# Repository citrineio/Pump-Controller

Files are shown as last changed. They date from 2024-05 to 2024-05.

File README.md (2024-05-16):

# Pump-Controller
This is the next version of the previously featured AC Switch. This is an IOT device that can turn normal water pumps smart. This device is meant to detect plumbing issues and automatically or allow the user to act. 
pump controller 2

## Features

 1. A wireless microcontroller (ESP32-C3-WROOM-02-N4) for remote monitoring and control of the pump.
 2.  40A SPDT relay with Quick Connect contacts (AZ2100-1CE-5DEF).
 3. 20A current transformer (ZMCT102) to detect when the pump is on by measuring motor current.
 4. A JST connector (B4B-PH-K) for a [pressure sensor](https://www.digikey.com/en/products/detail/seeed-technology-co-ltd/114991178/7387419)  to identify if the pump is pumping air.
 5. An AC/DC converter (PBO-5C-5 or equivalent) to supply power from an outlet.

## Block Diagram



## Future improvements

 1. Replace spring clamp terminal blocks with pluggable or screw terminals.
 2. Replace the JST connector with a pluggable terminal block.
 3. Replace TC2050 footprint and UART JST connector with 2.54mm footprints for use with a pogo pin probe clip (e.g. [This](https://www.adafruit.com/product/5434)).
 4. The board was designed with a specific enclosure in mind. Future revisions will have their own custom designed enclosure.
 5. Tagconnect cables without clamps are very inconvenient. 

Please let me know if you have any suggestions or improvements

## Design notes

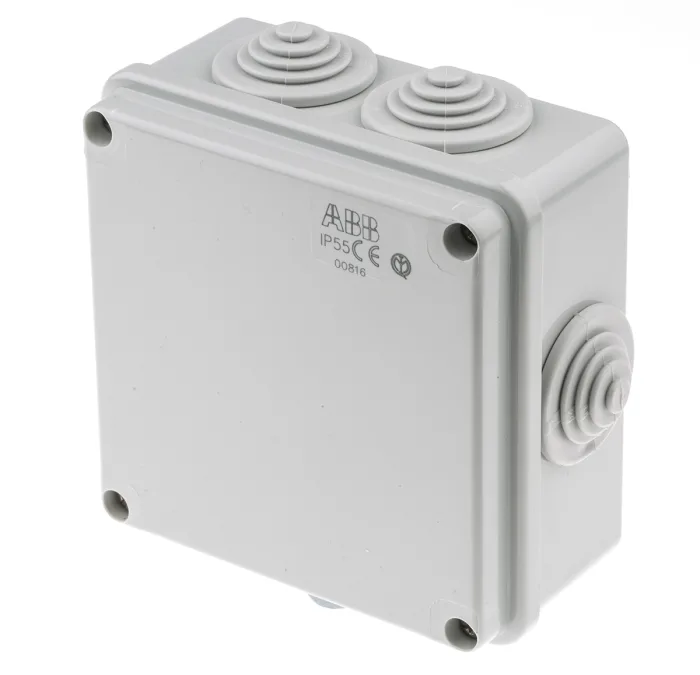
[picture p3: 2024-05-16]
V3.0/Mechanicals/Enclosure/F0454993-01.webp

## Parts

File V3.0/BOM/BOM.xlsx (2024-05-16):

# | Reference | Qty | Value | Footprint | DNP | Manufacturer | PN
1 | C3, C4, C5, C6 | 4 | 1u | parts:CAPC1608X90N_SAMSUNG |  | Samsung Electro-Mechanics | CL10B105KO8NNNC
2 | C7, C8 | 2 | 6P | parts:CAPC1608X90N_SAMSUNG |  | Samsung Electro-Mechanics | CL10C060DB8NNNC
3 | D1 | 1 | 1N4007FL | parts:CR_SOD-123FL_SME |  | SMC Diode Solutions | 1N4007FL
4 | H1, H2 | 2 | MountingHole | MountingHole:MountingHole_2.7mm_M2.5
5 | J1 | 1 | TB002-500-03BE | CUI_TB002-500-03BE |  | CUI Devices | TB002-500-03BE
6 | J2 | 1 | Conn_01x14 | Connector_PinHeader_2.54mm:PinHeader_1x08_P2.54mm_Vertical |  | Sullins Connector Solutions | PPTC141LFBN-RC
7 | K1 | 1 | G5LE-14 DC5 | Relay_THT:Relay_SPDT_Omron-G5LE-1 |  | OMRON | G5LE-14 DC5
8 | PS101 | 1 | HLK-PM01 | Converter_ACDC:Converter_ACDC_HiLink_HLK-PMxx |  | HI-LINK | HLK-PM01
9 | Q1 | 1 | Q_NMOS_GSD | parts:DMN65D8L-7_MOSFET |  | Diodes Incorporated | DMN65D8L-7
10 | R2, R3, R4 | 3 | 10K | parts:RESC1607X60N |  | YAGEO | RC0603JR-0710KL
11 | R5 | 1 | 10K | parts:RESC1607X60N | DNP | YAGEO | RC0603JR-0710KL
12 | RV1 | 1 | S14K350 | parts:VARS_B72214S_15P5X5P6-7P5-2P2_TDK |  | TDK | B72214S0351K101
13 | SW1 | 1 | TS-1187A-B-A-B | SW_TS-1187A-B-A-B |  | XKB Industrial Precision | TS-1187A-B-A-B
14 | SW2 | 1 | SW_SPDT | parts:SW_JS102011SAQN |  | C&K | JS102011SAQN
15 | U2 | 1 | AP2112K-3.3TRG1 | Package_TO_SOT_SMD:SOT-23-5 |  | Diodes Incorporated | AP2112K-3.3TRG1
16 | U3 | 1 | ESP32-C3-MINI-1U-H4 | parts:XCVR_ESP32-C3-MINI-1U-N4 |  | Espressif Systems | ESP32-C3-MINI-1U-H4
17 | Y1 | 1 | 32K768 | parts:XTAL_FC-135R_32.7680KA-AG0 |  | EPSON | FC-135R 32.7680KA-AG0

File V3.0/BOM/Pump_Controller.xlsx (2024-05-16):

Reference | Value | Qty | DNP | Manufacturer | Part Number
C101,C102,C103,C104,C105,C106,C108,C109,C115 | 1u | 9 |  | Samsung Electro-Mechanics | C15849
C110 | 10u | 1 |  | Samsung Electro-Mechanics | C96446
C111 | 22u | 1 |  | EPCOS - TDK Electronics | C160173
C112 | 470u | 1 |  | Kemet | C2887210
C113 | 100u | 1 |  | KEMET | C109392
C114 | 1n | 1 |  | Samsung | C651029
CR101 | SMBJ7.0CA-13-F | 1 |  | Diodes Incorporated | C7420377
D101 | 1N4007FL | 1 |  | SMC Diode Solutions | C64898
F101 | 56000001019 | 1 |  | Littelfuse Inc. | C206886
J101 | Screw_Terminal_01x02 | 1
J102,J105 | B4B-PH-K | 2 |  | JST | C131334
K101 | AZ2100-1CE-5DEF | 1 |  | American Zettler | C187900
L101 | 4m7 | 1 |  | Bourns | C6341414
L102 | 4u7 | 1 |  | Taiyo Yuden | C32684
PS101 | PBO-5C-5 | 1 |  | CUI Inc. | C784062
Q101,Q102,Q103,Q104 | C20917 | 4 |  | Alpha & Omega Semicon | C20917
R101,R103,R104,R109 | 10K | 4 |  | UNI-ROYAL(Uniroyal Elec) | C25804
R102 | 0R | 1 | DNP | UNI-ROYAL(Uniroyal Elec) | C21189
R106,R107,R108,R114,R115,R116 | 2k2 | 6 |  | UNI-ROYAL(Uniroyal Elec) | C4190
R113 | 12R | 1 |  | Yageo | C3013863
R118 | 68R | 1 |  | UNI-ROYAL(Uniroyal Elec) | C27592
R119 | 0R | 1 |  | UNI-ROYAL(Uniroyal Elec) | C21189
RV101 | B72214S0351K101 | 1 |  | B72214S0351K101 | B72214S0351K101
SW101 | SW_SPDT | 1 |  | XKB Connectivity | SS-12D10L3
SW102 | TS-1187A-B-A-B | 1 |  | XKB Industrial Precision | TS-1187A-B-A-B
TR102 | ZMCT102 | 1 |  | Qingxian Zeming Langxi Electronic | ZMCT102
U101 | ESP32-C3-WROOM | 1 |  | Espressif Systems | ESP32-C3-WROOM-02-N4
U102 | AP2112K-3.3 | 1 |  | Diodes Incorporated | AP2112K-3.3
U103 | ADS1115IDGSR | 1 |  | Texas Instruments | ADS1115IDGSR

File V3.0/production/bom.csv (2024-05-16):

Designator | Footprint | Quantity | Value | LCSC Part #
C101, C102, C103, C104, C105, C106, C108, C109, C115 | CL10A | 9 | 1u
C110 | CL10A | 1 | 10u
C111 | CP_Radial_D12.5mm_P5.00mm | 1 | 22u
C112 | CP_Radial_D6.3mm_P2.50mm | 1 | 470u
C113 | CP_Radial_D6.3mm_P2.50mm | 1 | 100u
C114 | CAP_CL31_SAM | 1 | 1n
CR101 | SMB_DIO | 1 | SMBJ7.0CA-13-F
D101 | SODFL3618X110N | 1 | 1N4007FL
F101 | FUSE_560_1019_LTF | 1 | 56000001019
H102, H103, H104 | MountingHole_3.2mm_M3 | 3 | MountingHole
J101 | CONN-TH_2P-P5.08_WJ142V-5.08-2P | 1 | Screw_Terminal_01x02
J102, J105 | JST_B4B-PH-K | 2 | B4B-PH-K
J103 | TAG-CONNECT_TC2050-IDC-NL | 1 | TC2050-IDC-NL
K101 | AZ2100-1CE-5DEF | 1 | AZ2100-1CE-5DEF
L101 | IND_RLB9012-472KL | 1 | 4m7
L102 | IND_HL4R7M_TAY | 1 | 4u7
PS101 | CONV_PBO-5C-5 | 1 | PBO-5C-5
Q101, Q102, Q103, Q104 | SOT-23 | 4 | DMG2302UK
R101, R103, R104, R109 | RESC1607X60N | 4 | 10K
R102, R119 | RESC1607X60N | 2 | 0R
R106, R107, R108, R114, R115, R116 | RESC1607X60N | 6 | 2k2
R113 | YAG_FMP200_YAG | 1 | 12R
R118 | RESC1607X60N | 1 | 68R
RV101 | VAR_B72214S0351K101 | 1 | B72214S0351K101
SW101 | SS12D10L3 | 1 | SW_SPDT
SW102 | SW_TS-1187A-B-A-B | 1 | TS-1187A-B-A-B
TR102 | zmct102 | 1 | ZMCT102
U101 | XCVR_ESP32-C3-WROOM-02U-N4 | 1 | ESP32-C3-WROOM
U102 | SOT95P285X140-5N | 1 | AP2112K-3.3
U103 | ADS1115_SOP50P490X110-10N | 1 | ADS1115IDGSR

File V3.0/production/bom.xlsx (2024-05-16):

Designator | Footprint | Quantity | Value | LCSC Part #
C101, C102, C103, C104, C105, C106, C108, C109, C115 | CL10A | 9 | 1u | C59782
C110 | CL10A | 1 | 10u | C96446
C111 | CP_Radial_D12.5mm_P5.00mm | 1 | 22u | C473184
C112 | CP_Radial_D6.3mm_P2.50mm | 1 | 470u | C2898811
C113 | CP_Radial_D6.3mm_P2.50mm | 1 | 100u | C495099
C114 | CAP_CL31_SAM | 1 | 1n | C3841467
CR101 | SMB_DIO | 1 | SMBJ7.0CA-13-F | C135095
D101 | SODFL3618X110N | 1 | 1N4007FL | C250817
F101 | FUSE_560_1019_LTF | 1 | 56000001019 | C142909
H102, H103, H104 | MountingHole_3.2mm_M3 | 3 | MountingHole
J101 | CONN-TH_2P-P5.08_WJ142V-5.08-2P | 1 |  | WJ142V-5.08-2P
J102, J105 | JST_B4B-PH-K | 2 | B4B-PH-K | C265289
J103 | TAG-CONNECT_TC2050-IDC-NL | 1 | TC2050-IDC-NL
K101 | AZ2100-1CE-5DEF | 1 | AZ2100-1CE-5DEF | AZ2100-1CE-5DEF
L101 | IND_RLB9012-472KL | 1 | 4m7 | RLB9012-472KL
L102 | IND_HL4R7M_TAY | 1 | 4u7 | LSXBD6060WHL4R7M
PS101 | CONV_PBO-5C-5 | 1 | PBO-5C-5 | C784062
Q101, Q102, Q103, Q104 | SOT-23 | 4 | DMG2302UK | C20917
R101, R103, R104, R109 | RESC1607X60N | 4 | 10K | C25804
R106, R107, R108, R114, R115, R116 | RESC1607X60N | 6 | 2k2 | C4190
R113 | YAG_FMP200_YAG | 1 | 12R | FMP200JR-52-12R
R118 | RESC1607X60N | 1 | 68R | C27592
R119 | RESC1607X60N | 1 | 0R | C21189
RV101 | VAR_B72214S0351K101 | 1 | B72214S0351K101 | B72214S0351K101
SW101 | SS12D10L3 | 1 | SW_SPDT | C319013
SW102 | SW_TS-1187A-B-A-B | 1 | TS-1187A-B-A-B | C318884
TR102 | zmct102 | 1 | ZMCT102 | C84213
U101 | XCVR_ESP32-C3-WROOM-02U-N4 | 1 | ESP32-C3-WROOM | C2934560
U102 | SOT95P285X140-5N | 1 | AP2112K-3.3 | C51118
U103 | ADS1115_SOP50P490X110-10N | 1 | ADS1115IDGSR | C37593

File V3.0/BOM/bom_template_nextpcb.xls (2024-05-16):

Manufacturer Part Number* | Qty* | Designator* | Customer Supply | Customer Remark
CL10B105KO8NNNC | 9 | C101,C102,C103,C104,C105,C106,C108,C109,C115
CL10A106MA8NRNC | 1 | C110
B43821F5226M000 | 1 | C111
SPZ1CM471E11O00RAXXX | 1 | C112
ESL107M035AE3AA | 1 | C113
CL31B102KHFNFNE | 1 | C114
SMBJ7.0CA-13-F | 1 | CR101
1N4007FL | 1 | D101
56000001019 | 1 | F101
WJ142V-5.08-2P | 1 | J101
B4B-PH-K | 2 | J102,J105
AZ2100-1CE-5DEF | 1 | K101
RLB9012-472KL | 1 | L101
LSXBD6060WHL4R7M | 1 | L102
LS05-13B05R3 | 1 | PS101
AO3400A | 4 | Q101,Q102,Q103,Q104
0603WAF1002T5E | 4 | R101,R103,R104,R109
0603WAF0000T5E | 1 | R102 | DNP
0603WAF2201T5E | 6 | R106,R107,R108,R114,R115,R116
FMP200JR-52-12R | 1 | R113
0603WAF680JT5E | 1 | R118
0603WAF0000T5E | 1 | R119
B72214S0351K101 | 1 | RV101
SS-12D10L3 | 1 | SW101
TS-1187A-B-A-B | 1 | SW102
ZMCT102 | 1 | TR102
ESP32-C3-WROOM-02-N4 | 1 | U101
AP2112K-3.3TRG1 | 1 | U102
ADS1115IDGSR | 1 | U103

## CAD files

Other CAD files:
V3.0/Mechanicals/Enclosure/LK-DR56.dwg
V3.0/Mechanicals/Enclosure/LK-PLC24 25B.dwg

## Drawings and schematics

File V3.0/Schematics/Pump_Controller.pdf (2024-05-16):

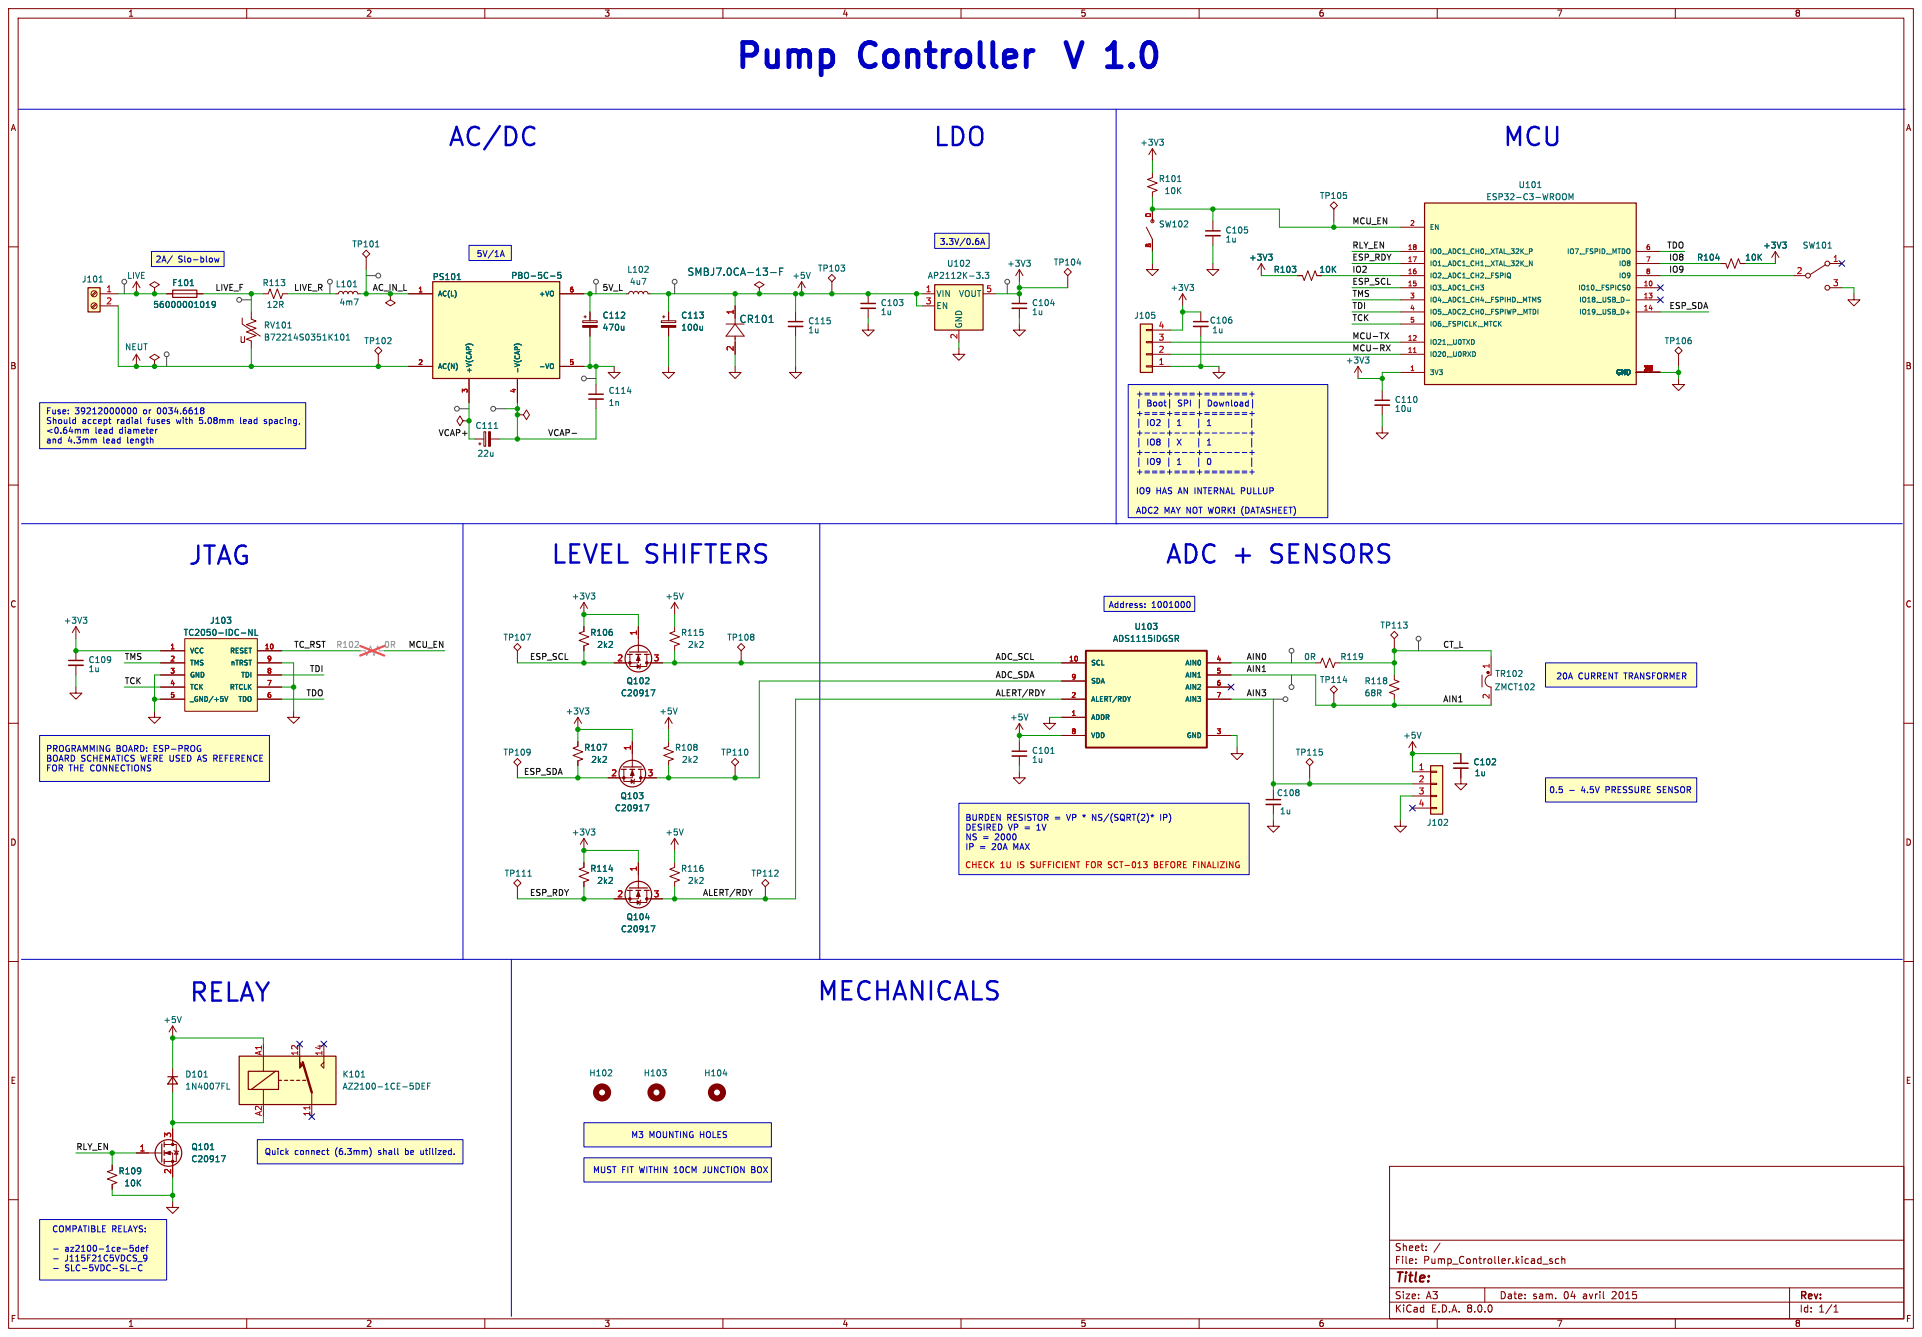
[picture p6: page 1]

IP = 20A MAX Pump Controller

IO9 HAS AN INTERNAL PULLUP
ADC + SENSORS

ADC2 MAY NOT WORK! (DATASHEET) M3 MOUNTING HOLES

PROGRAMMING BOARD: ESP-PROG
BOARD SCHEMATICS WERE USED AS REFERENCE

MUST FIT WITHIN 10CM JUNCTION BOX

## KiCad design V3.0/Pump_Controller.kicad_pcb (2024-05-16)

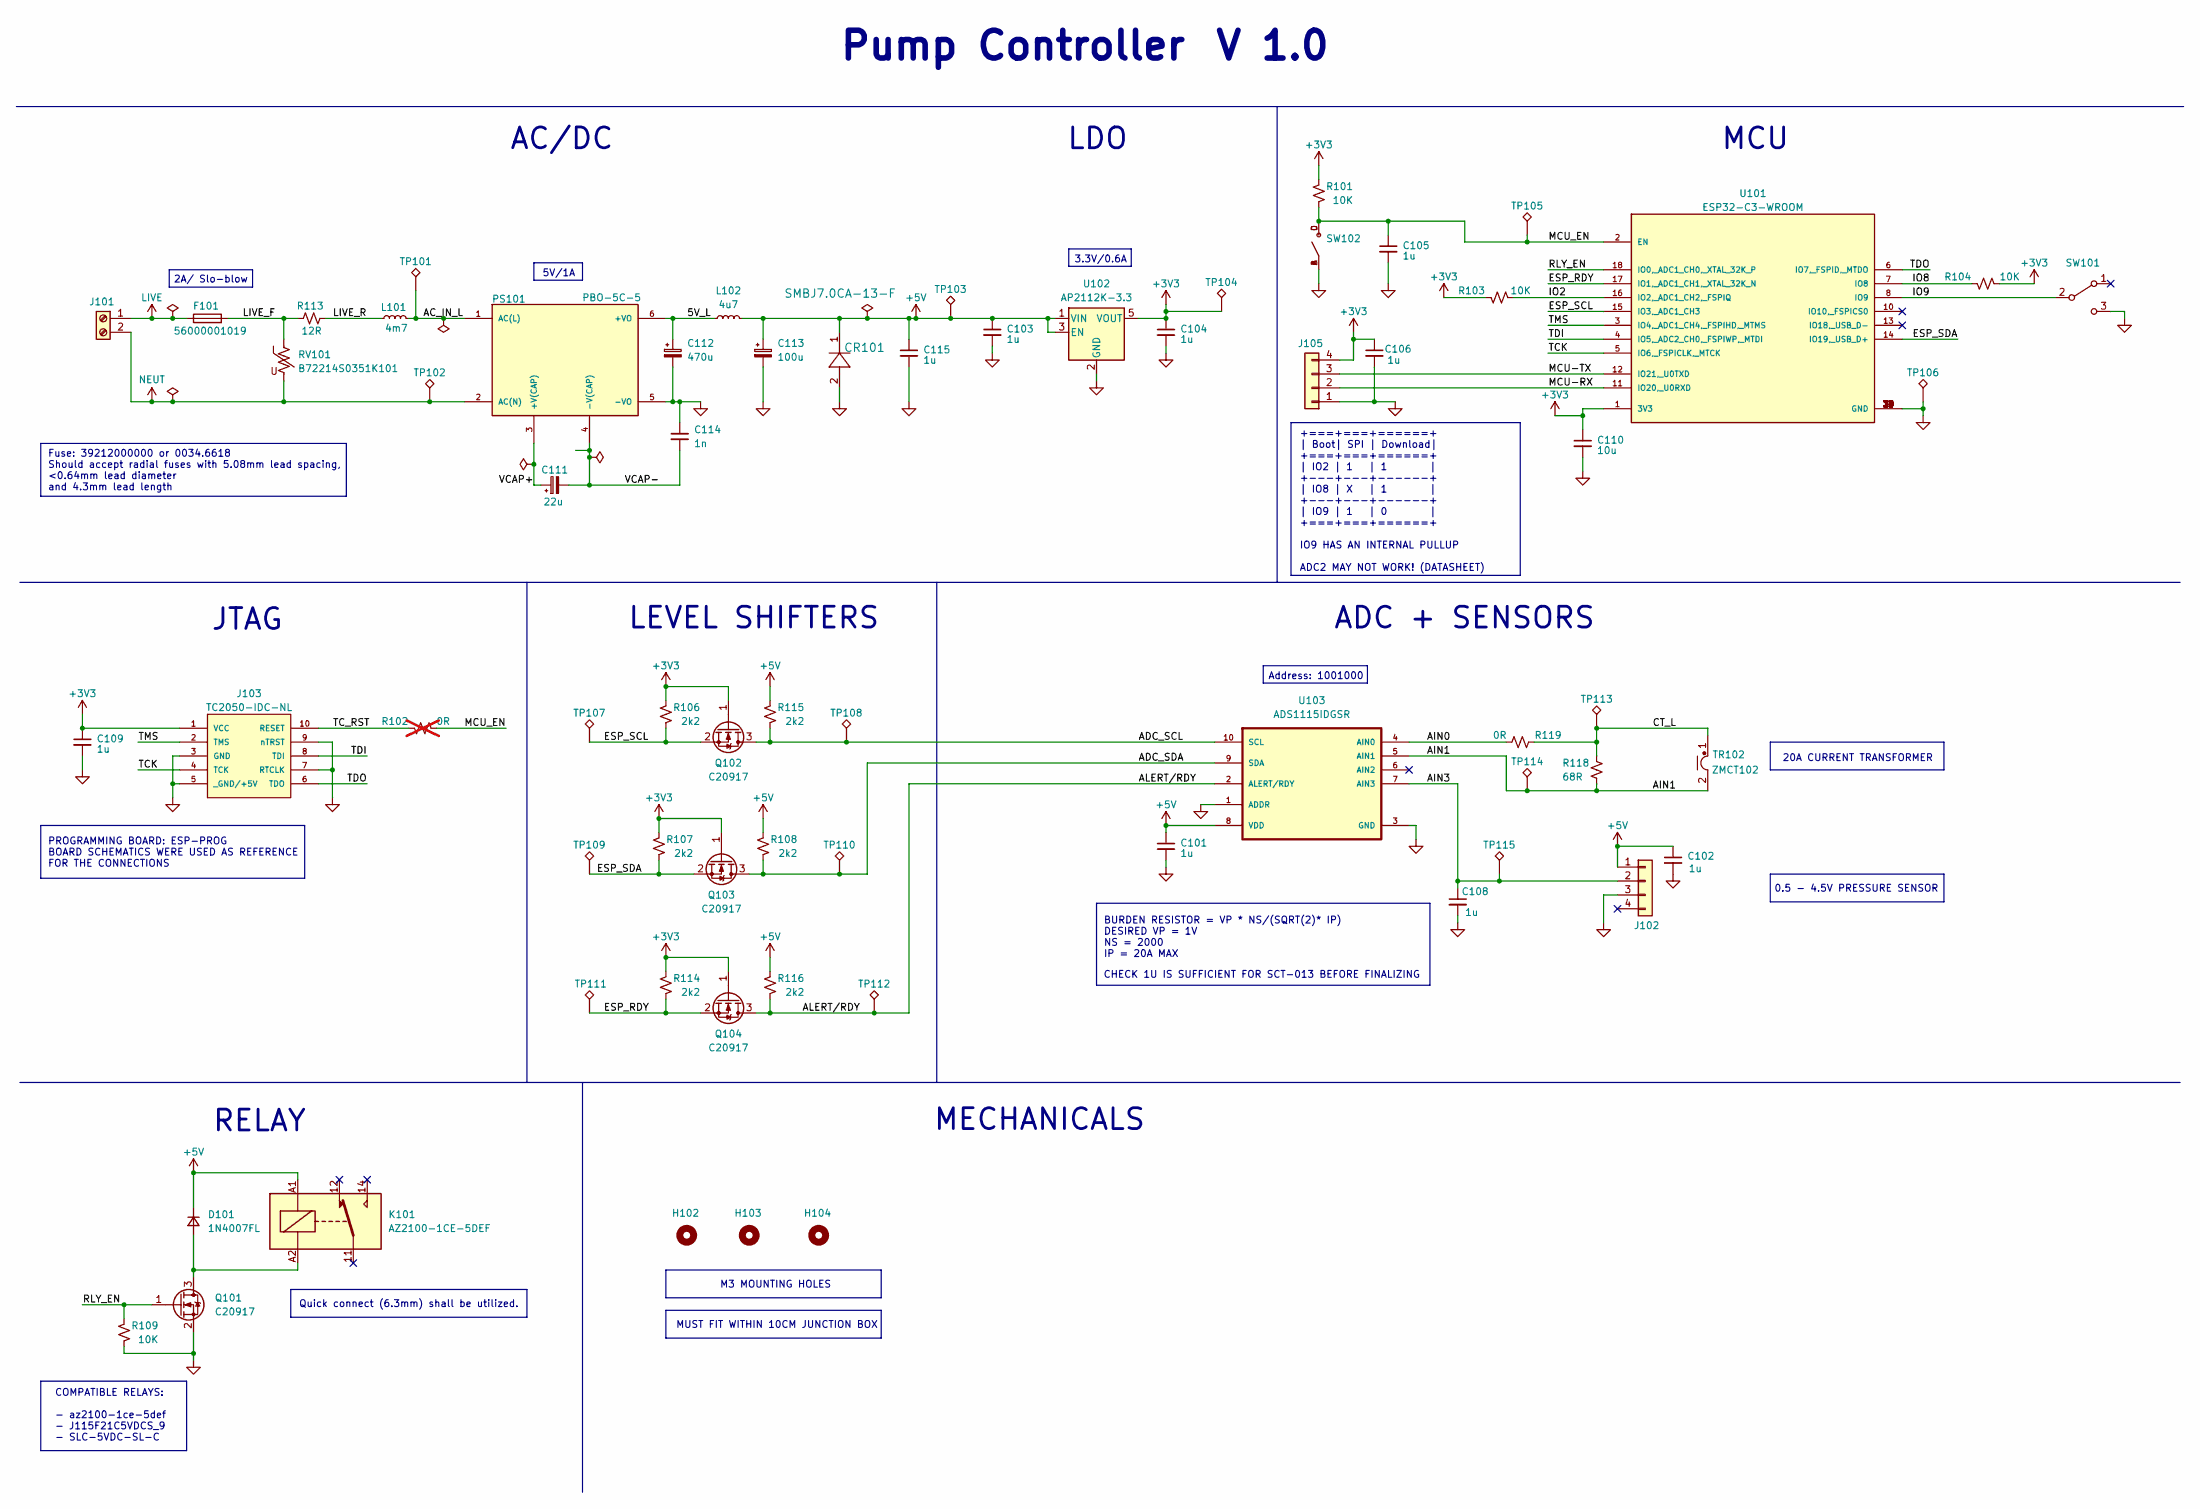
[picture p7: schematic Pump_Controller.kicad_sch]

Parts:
C101, C102, C103, C104, C105, C106, C108, C109, C115: 1u; CL10A; Part Number CL10B105KO8NNNC - C59782
C110: 10u; CL10A; Part Number CL10A106MA8NRNC - C96446
C111: 22u; CP_Radial_D12.5mm_P5.00mm; Part Number B43821F5226M000
C112: 470u; CP_Radial_D6.3mm_P2.50mm; Part Number A750EQ477M1CAAE015
C113: 100u; CP_Radial_D6.3mm_P2.50mm; Part Number ESL107M035AE3AA
C114: 1n; CAP_CL31_SAM; Part Number CL31B102KHFNFNE
CR101: SMBJ7.0CA-13-F; SMB_DIO; Part Number SMBJ7.0CA-13-F
D101: 1N4007FL; SODFL3618X110N; Part Number 1N4007FL
F101: 56000001019; FUSE_560_1019_LTF; Part Number 56000001019
H102, H103, H104: MountingHole; MountingHole_3.2mm_M3
J101: Screw_Terminal_01x02; CONN-TH_2P-P5.08_WJ142V-5.08-2P
J102, J105: B4B-PH-K; JST_B4B-PH-K; Part Number B4B-PH-K
J103: TC2050-IDC-NL; TAG-CONNECT_TC2050-IDC-NL
K101: AZ2100-1CE-5DEF; Part Number AZ2100-1CE-5DEF
L101: 4m7; IND_RLB9012-472KL; Part Number RLB9012-472KL
L102: 4u7; IND_HL4R7M_TAY; Part Number LSXBD6060WHL4R7M
PS101: PBO-5C-5; CONV_PBO-5C-5; Part Number PBO-5C-5
Q101, Q102, Q103, Q104: C20917; SOT-23; Part Number AO3400A
R101, R103, R104, R109: 10K; RESC1607X60N; Part Number 0603WAF1002T5E - C25804
R102: 0R; RESC1607X60N; Part Number 0603WAF0000T5E - C21189; not fitted
R106, R107, R108, R114, R115, R116: 2k2; RESC1607X60N; Part Number 0603WAF2201T5E- C4190
R113: 12R; YAG_FMP200_YAG; Part Number FMP200JR-52-12R
R118: 68R; RESC1607X60N; Part Number 0603WAF680JT5E- C27592
R119: 0R; RESC1607X60N; Part Number 0603WAF0000T5E - C21189
RV101: B72214S0351K101; VAR_B72214S0351K101; Part Number B72214S0351K101
SW101: SW_SPDT; SS12D10L3; Part Number SS-12D10L3
SW102: TS-1187A-B-A-B; SW_TS-1187A-B-A-B; Part Number TS-1187A-B-A-B
TP101, TP102: TestPoint_Alt; TestPoint_Loop_D2.50mm_Drill1.0mm
TP103, TP104, TP105, TP106, TP107, TP108, TP109, TP110, TP111, TP112, TP113, TP114, TP115: TestPoint_Alt; TestPoint_Pad_1.5x1.5mm
TR102: ZMCT102; zmct102; Part Number ZMCT102
U101: ESP32-C3-WROOM; XCVR_ESP32-C3-WROOM-02U-N4; Part Number ESP32-C3-WROOM-02-N4
U102: AP2112K-3.3; SOT95P285X140-5N; Part Number AP2112K-3.3
U103: ADS1115IDGSR; ADS1115_SOP50P490X110-10N; Part Number ADS1115IDGSR

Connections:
+3V3: C104.1, C106.1, C109.1, C110.1, J103.1 (VCC), J105.4, Q102.1 (G), Q103.1 (G), Q104.1 (G), R101.1, R103.1, R104.2, R106.1, R107.1, R114.1, TP104.1, U101.1 (3V3), U102.5 (VOUT)
+5V: C101.1, C102.1, C103.1, C113.1, C115.1, CR101.1, D101.1 (K), J102.1, K101.A1, L102.2, R108.1, R115.1, R116.1, TP103.1, U102.1 (VIN), U102.3 (EN), U103.8 (VDD)
/5V_L: C112.1, L102.1, PS101.6 (+VO)
/AC_IN_L: L101.2, PS101.1 (AC(L)), TP101.1
/ADC_SCL: Q102.3 (D), R115.2, TP108.1, U103.10 (SCL)
/ADC_SDA: Q103.3 (D), R108.2, TP110.1, U103.9 (SDA)
/AIN0: R119.2, U103.4 (AIN0)
/AIN1: R118.2, TP114.1, TR102.2, U103.5 (AIN1)
/AIN3: C108.1, J102.2, TP115.1, U103.7 (AIN3)
/ALERT/RDY: Q104.3 (D), R116.2, TP112.1, U103.2 (ALERT/RDY)
/CT_L: R118.1, R119.1, TP113.1, TR102.1
/ESP_RDY: Q104.2 (S), R114.2, TP111.1, U101.17 (IO1,_ADC1_CH1,_XTAL_32K_N)
/ESP_SCL: Q102.2 (S), R106.2, TP107.1, U101.15 (IO3,_ADC1_CH3)
/ESP_SDA: Q103.2 (S), R107.2, TP109.1, U101.14 (IO19,_USB_D+)
/IO2: R103.2, U101.16 (IO2,_ADC1_CH2,_FSPIQ)
/IO8: R104.1, U101.7 (IO8)
/IO9: SW101.2 (B), U101.8 (IO9)
/LIVE_F: F101.2, R113.1, RV101.1
/LIVE_R: L101.1, R113.2
/MCU-RX: J105.2, U101.11 (IO20,_U0RXD)
/MCU-TX: J105.3, U101.12 (IO21,_U0TXD)
/MCU_EN: C105.1, R101.2, R102.2, SW102.C, SW102.D, TP105.1, U101.2 (EN)
/RLY_EN: Q101.1 (G), R109.1, U101.18 (IO0,_ADC1_CH0,_XTAL_32K_P)
/TCK: J103.4 (TCK), U101.5 (IO6,_FSPICLK,_MTCK)
/TC_RST: J103.10 (RESET), R102.1
/TDI: J103.8 (TDI), U101.4 (IO5,_ADC2_CH0,_FSPIWP,_MTDI)
/TDO: J103.6 (TDO), U101.6 (IO7,_FSPID,_MTDO)
/TMS: J103.2 (TMS), U101.3 (IO4,_ADC1_CH4,_FSPIHD,_MTMS)
/VCAP+: C111.1, PS101.3 (+V(CAP))
/VCAP-: C111.2, C114.2, PS101.4 (-V(CAP))
GND: C101.2, C102.2, C103.2, C104.2, C105.2, C106.2, C108.2, C109.2, C110.2, C112.2, C113.2, C114.1, C115.2, CR101.2, J102.3, J103.3 (GND), J103.5 (_GND/+5V), J103.7 (RTCLK), J103.9 (nTRST), J105.1, PS101.5 (-VO), Q101.2 (S), R109.2, SW101.3 (C), SW102.A, SW102.B, TP106.1, U101.9 (GND), U101.19 (GND), U101.20 (GND), U101.21 (GND), U101.22 (GND), U101.23 (GND), U101.24 (GND), U101.25 (GND), U101.26 (GND), U101.27 (GND), U101.28 (GND), U101.29 (GND), U101.30 (GND), U101.31 (GND), U101.32 (GND), U101.33 (GND), U101.34 (GND), U101.35 (GND), U101.36 (GND), U101.37 (GND), U101.38 (GND), U101.39 (GND), U102.2 (GND), U103.1 (ADDR), U103.3 (GND)
LIVE: F101.1, J101.1
NEUT: J101.2, PS101.2 (AC(N)), RV101.2, TP102.1
unnamed: D101.2 (A), K101.A2, Q101.3 (D)

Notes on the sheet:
+===+===+======+ | Boot| SPI | Download| +===+===+======+ | IO2 | 1 | 1 | +---+---+------+ | IO8 | X | 1 | +---+---+------+ | IO9 | 1 | 0 | +===+===+======+ IO9 HAS AN INTERNAL PULLUP ADC2 MAY NOT WORK! (DATASHEET)
5V/1A
0.5 - 4.5V PRESSURE SENSOR
LEVEL SHIFTERS
Quick connect (6.3mm) shall be utilized.
3.3V/0.6A
AC/DC
MUST FIT WITHIN 10CM JUNCTION BOX
RELAY
COMPATIBLE RELAYS: - az2100-1ce-5def - J115F21C5VDCS_9 - SLC-5VDC-SL-C
BURDEN RESISTOR = VP * NS/(SQRT(2)* IP) DESIRED VP = 1V NS = 2000 IP = 20A MAX
PROGRAMMING BOARD: ESP-PROG BOARD SCHEMATICS WERE USED AS REFERENCE FOR THE CONNECTIONS
JTAG
M3 MOUNTING HOLES
20A CURRENT TRANSFORMER
Pump Controller
LDO
Fuse: 39212000000 or 0034.6618 Should accept radial fuses with 5.08mm lead spacing, <0.64mm lead diameter and 4.3mm lead length
Address: 1001000
CHECK 1U IS SUFFICIENT FOR SCT-013 BEFORE FINALIZING
MECHANICALS
2A/ Slo-blow
MCU
ADC + SENSORS
V 1.0

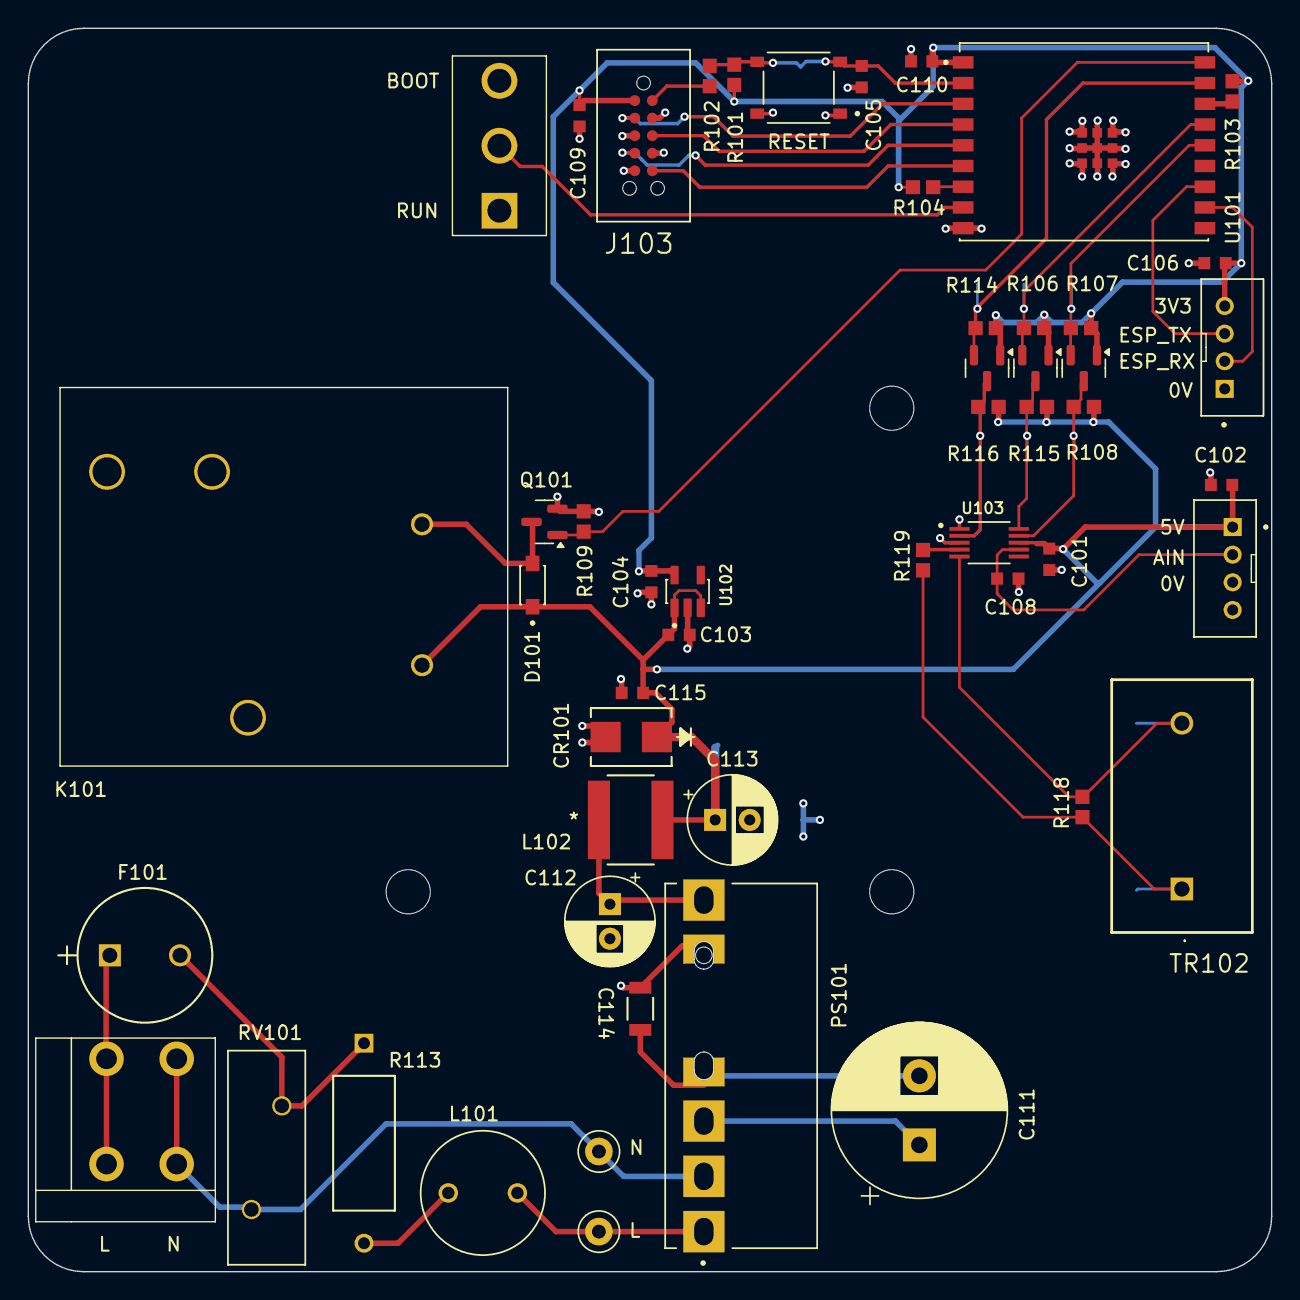
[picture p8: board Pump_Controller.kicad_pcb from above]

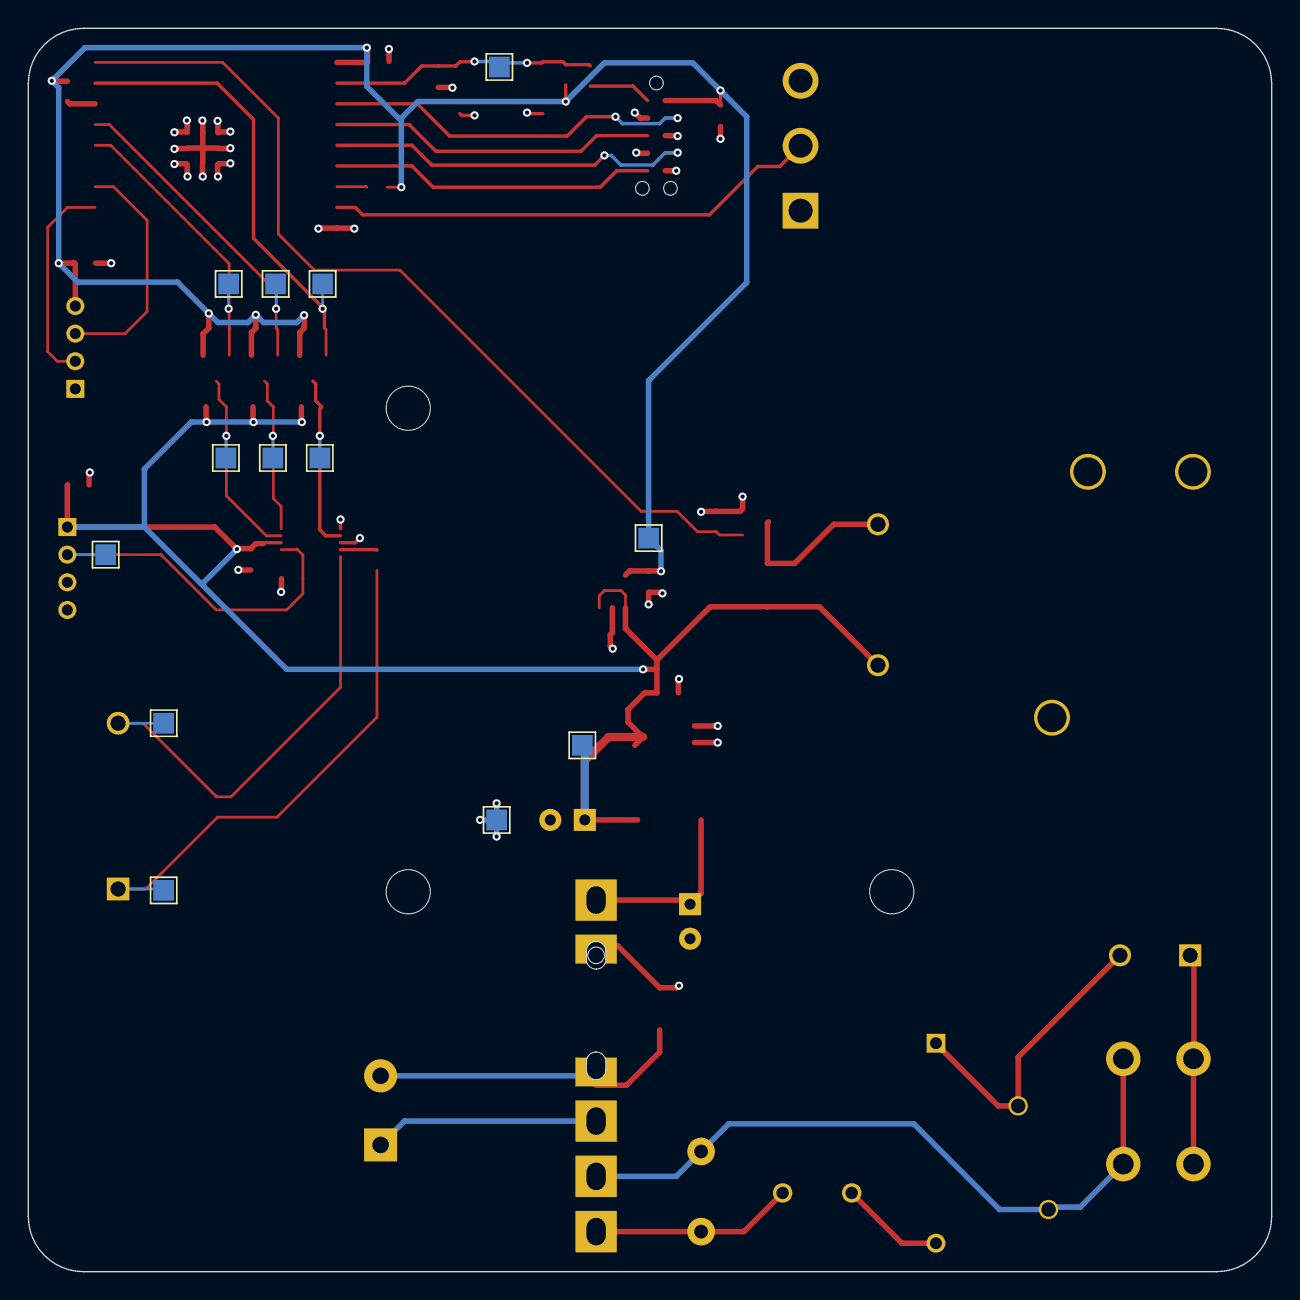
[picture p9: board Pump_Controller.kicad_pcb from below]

Board: 4 copper layers, 90.0 x 90.0 mm, 68 parts (13 on the bottom side), 34 nets.

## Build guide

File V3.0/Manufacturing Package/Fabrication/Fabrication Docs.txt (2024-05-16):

- Silk Screen (Legend)
- Solder Paste
- Solder Mask
- Copper Layers
- Outline
- Drills (PTH and NPTH)
- Drills Map
- Fabrication Drawing in PDF(Board, dimensions, stackup, fab notes)

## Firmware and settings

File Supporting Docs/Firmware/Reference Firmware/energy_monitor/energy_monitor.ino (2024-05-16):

#include "EmonLib.h"
// Include Emon Library
EnergyMonitor emon1;
int state = 0;
char relay = ' ';
// Create an instance
void setup()
{
  Serial.begin(9600);
  
  emon1.current(1, 30);             // Current: input pin, calibration.
  pinMode(2, OUTPUT);

  digitalWrite(2, LOW); 

}

void loop()
{
while (Serial.available()){
  double Irms = emon1.calcIrms(1480);  // Calculate Irms only
  Serial.print(" ");
  state = Serial.read();
  digitalWrite(2, relay); 
  if(Irms > 0.11){
  Serial.println("Bulb On");
}
else {
  Serial.println("Bulb Off");
}
  Serial.println(Irms);		       // Irms
}

  


}
// This code works and outputs 0.15A for a 150mA light bulb
